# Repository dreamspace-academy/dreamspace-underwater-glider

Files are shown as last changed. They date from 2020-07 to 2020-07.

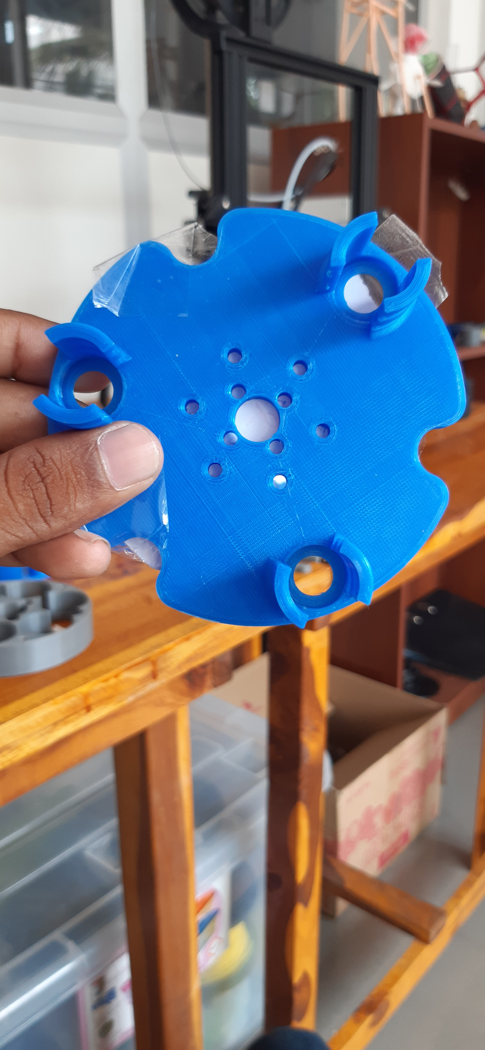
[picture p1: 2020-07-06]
images/printing-parts/underwater-glider-dreamspace-21.jpg

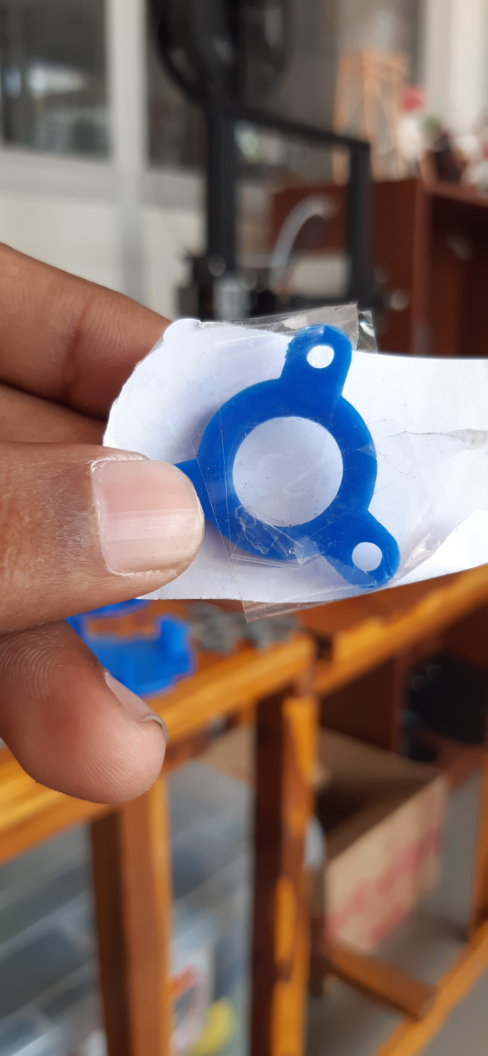
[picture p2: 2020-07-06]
images/printing-parts/underwater-glider-dreamspace-23.jpg

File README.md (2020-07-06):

# Underwater Glider



## **Motivation**

### Blue Econemy
Sri Lanka is an island country, located in the Indian Ocean, with a coastline of 1,585 km long, and the country claims an Exclusive Economic Zone (EEZ) extending 200 nautical miles, which is approximately 6.7 times Sri Lanka's land area. [1]

### Life Below Water
The world’s waters – their temperature, chemistry, currents and life – drive global systems that make the Earth habitable. How we manage this vital resource is essential for life on earth, and to counterbalance the effects of climate change. [2]

## **Problem**

### Real-time Monitoring
To keep our water ecosystem safe, secure, clean and sustainable, we need to measure various parameters in real-time. Sri Lanka, being a country that was devastated by 30 years of war, doesn’t even have the basic infrastructure, such as roads, in many parts of the country.

Therefore it is understandable that there is no modern infrastructure in Sri Lanka to measure and monitor the water ecosystems. Such equipment is very crucial for scientific research and assessment on an ecosystem, which is swiftly changing due to various weather conditions. [3]

### Affordability
The coastline and adjacent waters support highly productive marine ecosystems, and provide a massive economic value to this small nation, while this unique geographical position is highly contested by global powers.

## **Solution**

### Open-source Underwater Glider (OSUG)
There has been a breakthrough with low cost autonomous underwater vehicles, and as this capability has matured a wide range of hobby and commercial applications have been developed. However, there are no affordable extended duration underwater exploration platforms and this project aims to address this need.

Alex Williams, a young innovator from the USA, has developed a low cost and versatile underwater glider capable of extended missions of up to weeks at a time; using commodity hardware, 3D printed parts and an open-source autopilot. Furthermore, he won the Grand Prize in the Hackaday Prize Challenge 2017. [4]

### Underwater Gliding
Underwater gliders use a buoyancy engine to change the mass of the glider, allowing them to ascend and descend through the water. With power only being used to power the engine intermittently, gliders can typically run for weeks or months without recharge, making them ideal for environmental monitoring. As underwater gliders travel slowly through the water, they disturb the surrounding water very little, allowing for accurate and reliable data recording. [5]

underwater-glider-shanjeevan-dreamspace-7 (1)

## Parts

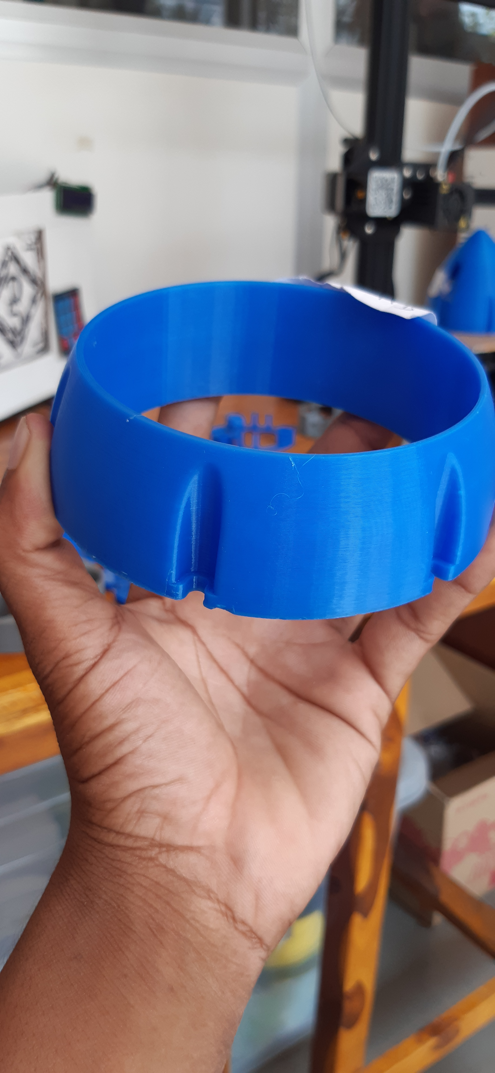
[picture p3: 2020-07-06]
images/printing-parts/underwater-glider-dreamspace-28.jpg

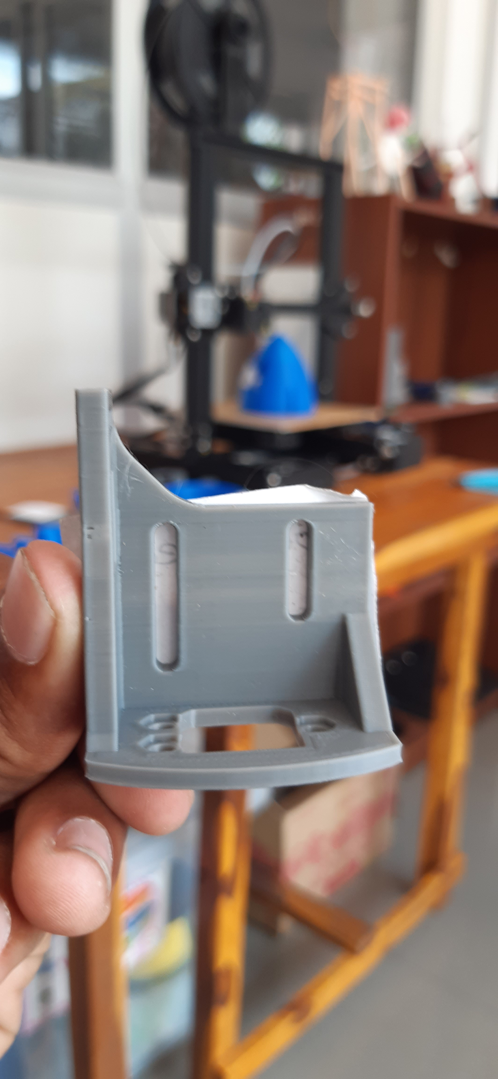
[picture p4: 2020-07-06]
images/printing-parts/underwater-glider-dreamspace-6.jpg

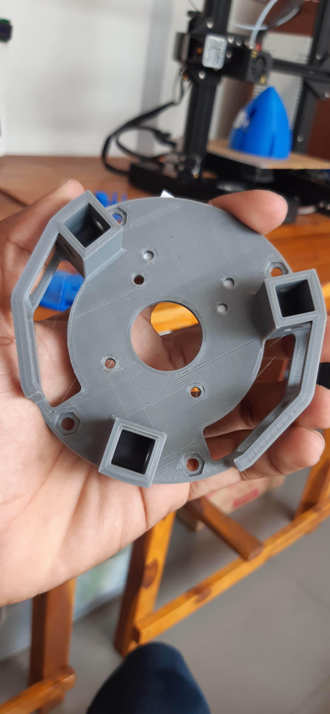
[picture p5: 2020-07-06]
images/printing-parts/underwater-glider-dreamspace-30.jpg

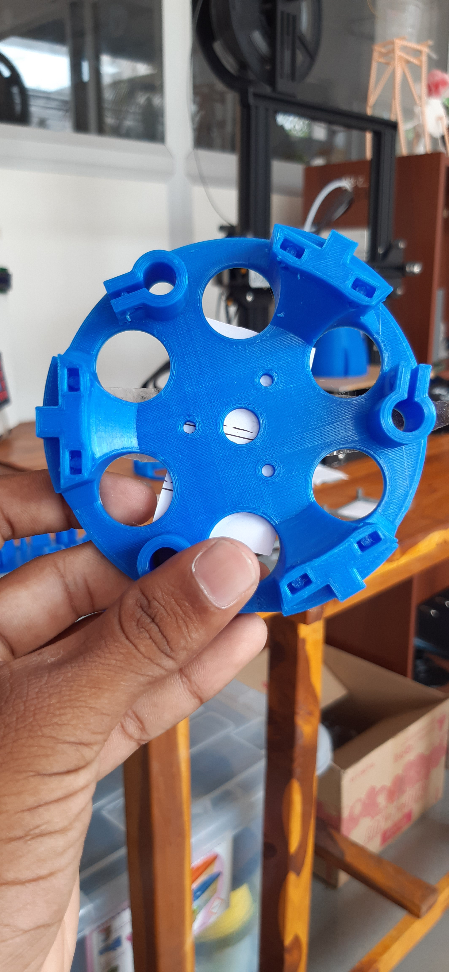
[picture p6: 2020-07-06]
images/printing-parts/underwater-glider-dreamspace-24.jpg

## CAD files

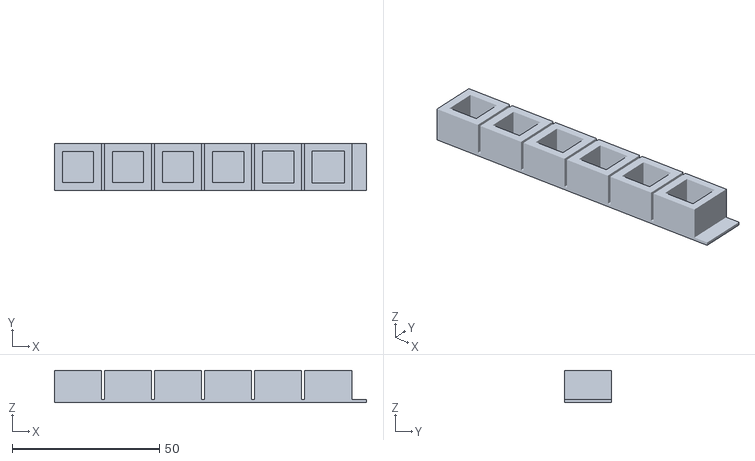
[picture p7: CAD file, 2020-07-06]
manufacture/3d-printing-parts/test-pieces/test-pieces-alum-tubing.stl
106.0 x 16.0 x 11.0

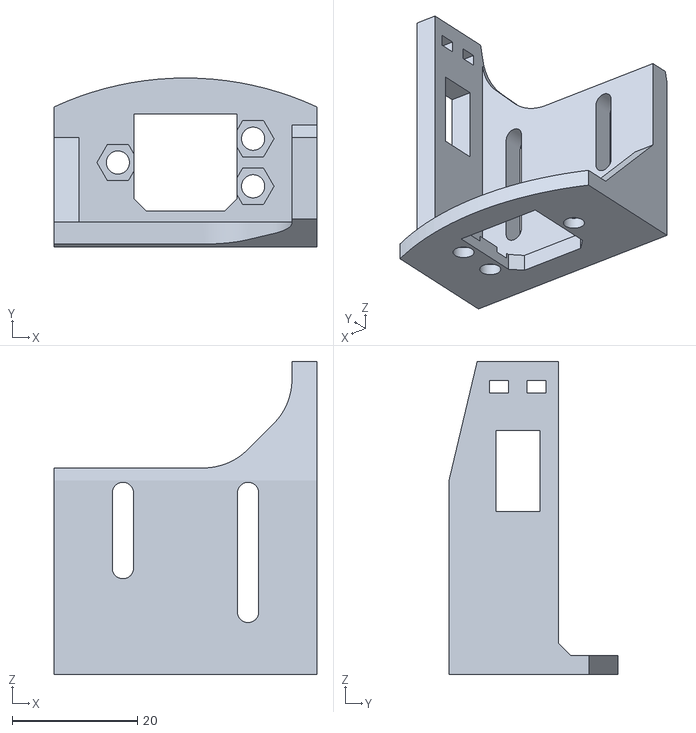
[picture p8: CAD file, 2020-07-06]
manufacture/3d-printing-parts/pogo-header-back-mount.stl
42.0 x 27.0 x 50.0

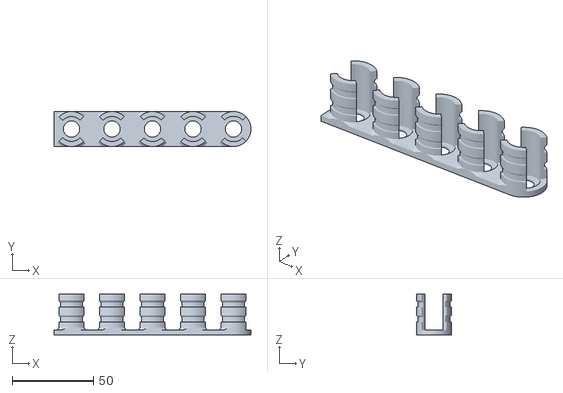
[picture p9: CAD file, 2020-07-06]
manufacture/3d-printing-parts/test-pieces/test-pieces-lm8uu.stl
121.6 x 21.6 x 25.0

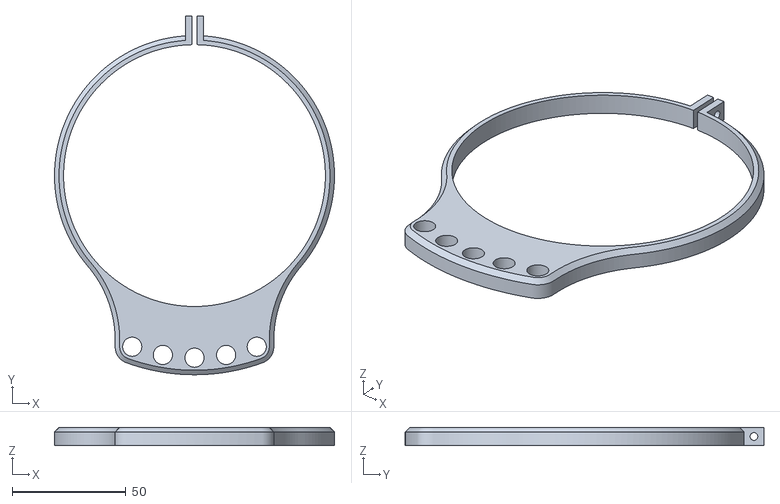
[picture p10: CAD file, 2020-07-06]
manufacture/3d-printing-parts/exterior-bar-mount.stl
123.0 x 157.5 x 8.00

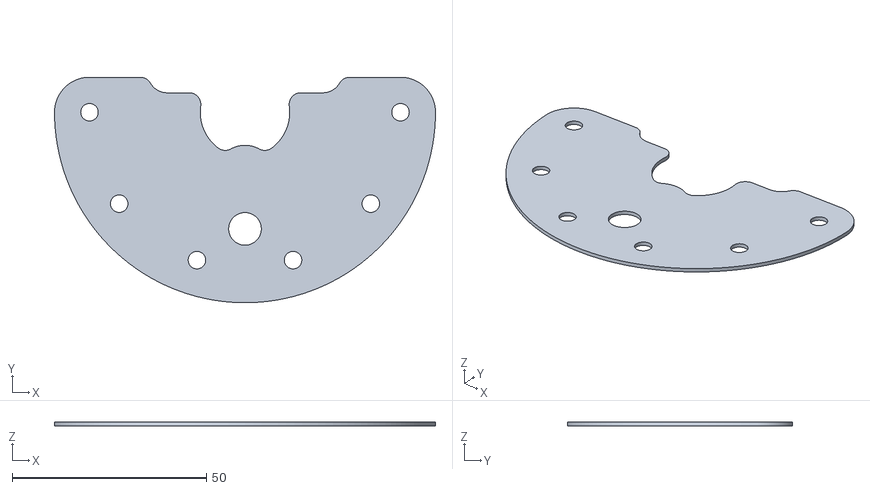
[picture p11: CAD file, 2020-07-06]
manufacture/3d-printing-parts/battery-rods-cover.stl
98.0 x 58.0 x 1.00

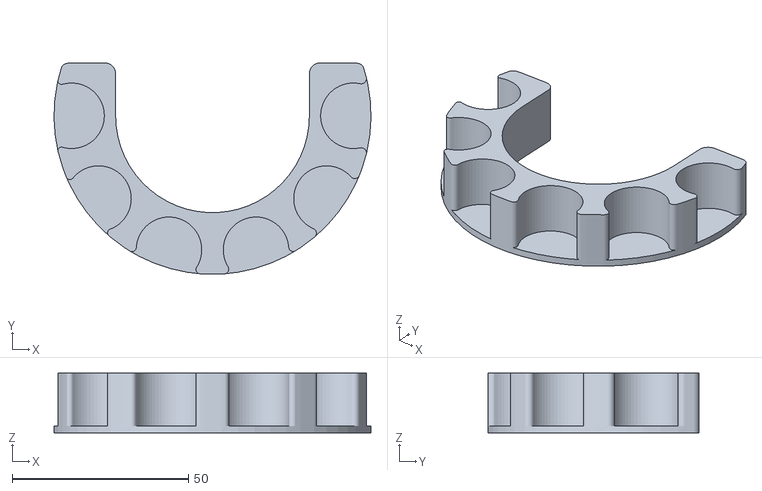
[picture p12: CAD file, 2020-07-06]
manufacture/3d-printing-parts/test-pieces/test-pieces-18650-fillet.stl
90.0 x 59.9 x 17.0

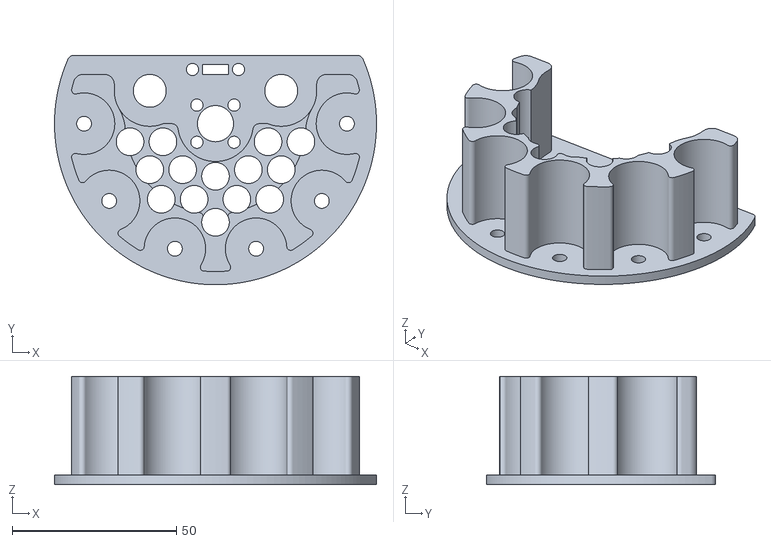
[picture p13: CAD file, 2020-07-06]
manufacture/3d-printing-parts/battery-mount-acme.stl
98.0 x 69.8 x 33.0

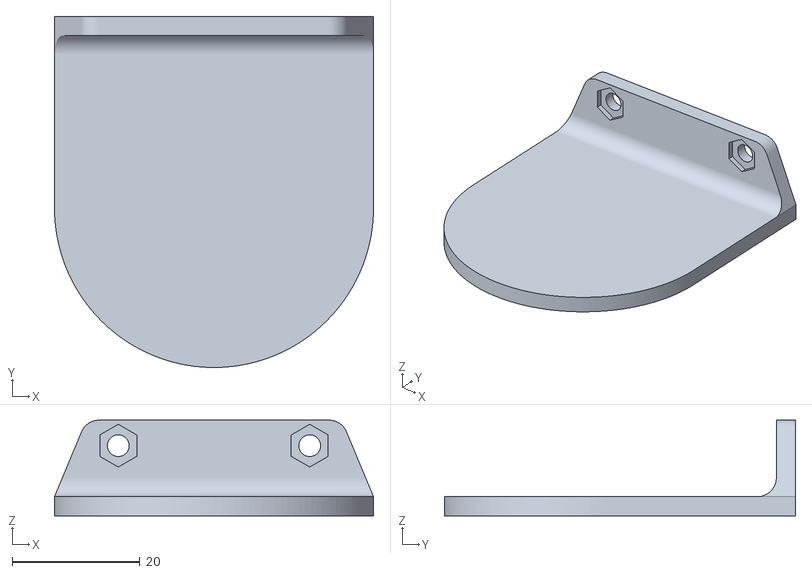
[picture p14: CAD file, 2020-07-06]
manufacture/3d-printing-parts/gps-mounting-plate.stl
50.0 x 55.0 x 15.0

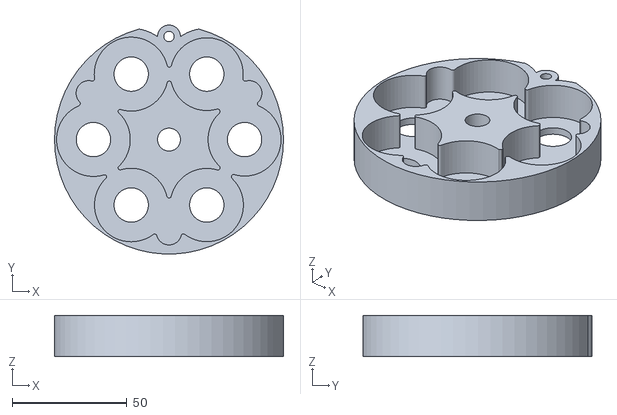
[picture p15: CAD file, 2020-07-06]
manufacture/3d-printing-parts/test-pieces/test-pieces-syringes.stl
100.0 x 99.9 x 18.0

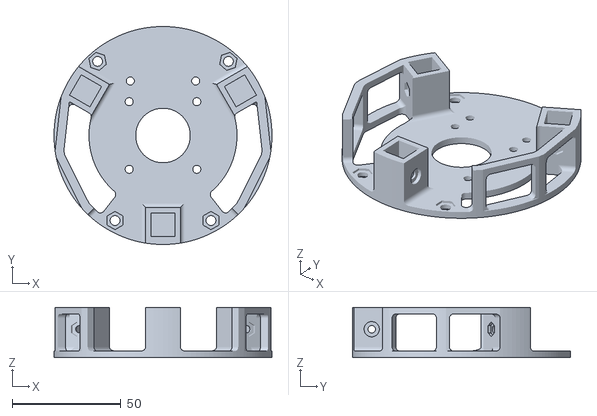
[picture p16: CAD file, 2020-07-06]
manufacture/3d-printing-parts/roll-motor-mount.stl
100.0 x 100.0 x 23.0

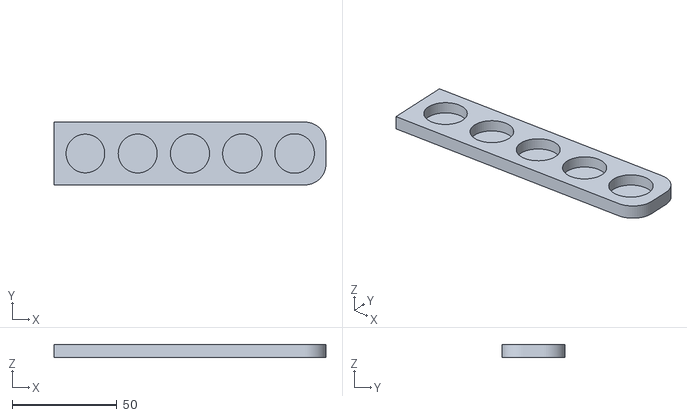
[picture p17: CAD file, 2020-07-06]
manufacture/3d-printing-parts/test-pieces/test-pieces-18650-diam.stl
130.0 x 30.0 x 6.00

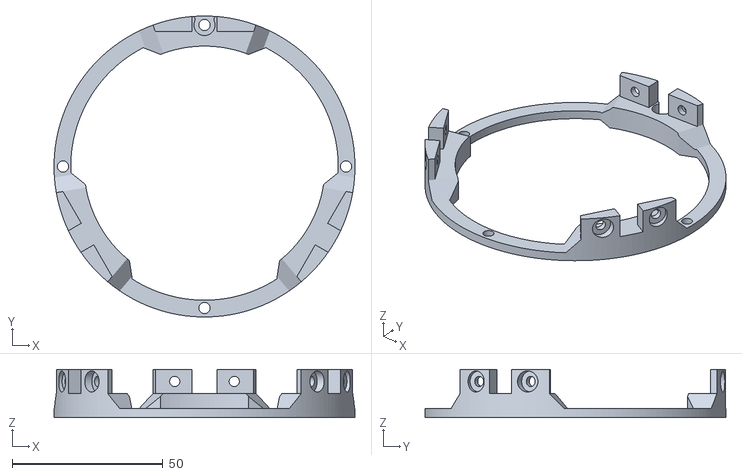
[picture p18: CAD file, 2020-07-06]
manufacture/3d-printing-parts/engine-endcap-mount.stl
100.0 x 100.0 x 16.0

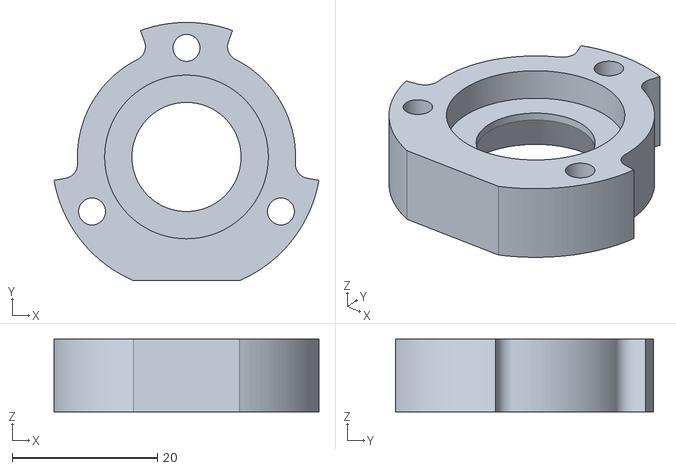
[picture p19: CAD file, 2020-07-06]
manufacture/3d-printing-parts/acme-bearing-back.stl
36.4 x 35.5 x 10.0

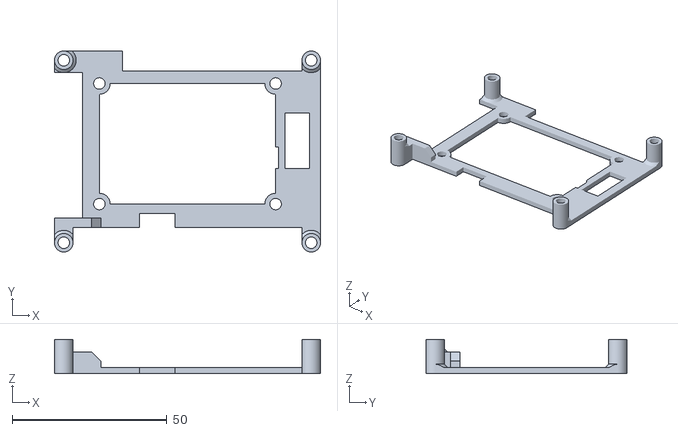
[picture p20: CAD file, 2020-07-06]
manufacture/3d-printing-parts/fathom-s-mounting-bracket.stl
86.0 x 65.0 x 11.0

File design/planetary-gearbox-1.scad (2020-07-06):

// Planetary gear bearing (customizable)

//

// clearance
tol=0.25;


M3_bolt_v_diam = 3.4;

M4_bolt_h_diam = 4.7;

M3_nut_v_diam = 6.7;


//End of edittable values

total_diameter_of_gearbox = 100;
// outer diameter of ring
D=75;
// thickness
T=10;

number_of_planets=3;
number_of_teeth_on_planets=7    ;
approximate_number_of_teeth_on_sun=11;
// pressure angle
P=45;//[30:60]
// number of teeth to twist across
nTwist=0.4;
// width of hexagonal hole
w=6.7;

DR=0.5*1;// maximum depth ratio of teeth

m=round(number_of_planets);
np=round(number_of_teeth_on_planets);
ns1=approximate_number_of_teeth_on_sun;
k1=round(2/m*(ns1+np));
k= k1*m%2!=0 ? k1+1 : k1;
ns=k*m/2-np;
echo(ns);
nr=ns+2*np;
pitchD=0.9*D/(1+min(PI/(2*nr*tan(P)),PI*DR/nr));
pitch=pitchD*PI/nr;
echo(pitch);
helix_angle=atan(2*nTwist*pitch/T);
echo(helix_angle);

phi=$t*360/m;


translate([0,0,10]){
    difference(){
        intersection(){
            difference(){
                cylinder(r=total_diameter_of_gearbox/2, h=20, center=true, $fn=100); 
                cylinder(r=D/2,h=50,center=true,$fn=100);
            }
            union(){
                translate([total_diameter_of_gearbox/2,0,0]){
                    cylinder(r=total_diameter_of_gearbox/2, h=50, center=true, $fn=6);
                }
                mirror([1,0,0]){
                    translate([total_diameter_of_gearbox/2,0,0]){
                        cylinder(r=total_diameter_of_gearbox/2, h=50, center=true, $fn=4);
                    }
                }
            }
        }
        
    translate([34,30,-15]){
        cylinder(r=M4_bolt_h_diam/2, h=30, $fn=100);
    }
    mirror([0,1,0]){
        translate([34,30,-15]){
            cylinder(r=M4_bolt_h_diam/2, h=30, $fn=100);
        }
    }
    translate([-39,22,-15]){
        cylinder(r=M4_bolt_h_diam/2, h=30, $fn=100);
    }
    mirror([0,1,0]){
        translate([-39,22,-15]){
            cylinder(r=M4_bolt_h_diam/2, h=30, $fn=100);
        }
    }
    }
}


  
translate([0,0,T/2]){
        union(){
            difference(){
                cylinder(r=D/2,h=T,center=true,$fn=100);
                herringbone(nr,pitch,P,DR,-tol,helix_angle,T+0.2,false);
                difference(){
                    translate([0,-D/2,0])rotate([90,0,0])monogram(h=10);
                    cylinder(r=D/2-0.25,h=T+2,center=true,$fn=100);
                }
            }
            rotate([0,0,(np+1)*180/ns+phi*(ns+np)*2/ns])
            difference(){
                mirror([0,1,0])
                    herringbone(ns,pitch,P,DR,tol,helix_angle,T,true);
                cylinder(r=2.5,h=50,center=true,$fn=100);
            }
            for(i=[1:m])rotate([0,0,i*360/m+phi])translate([pitchD/2*(ns+np)/nr,0,0])
                rotate([0,0,i*ns/m*360/np-phi*(ns+np)/np-phi])
                    herringbone(np,pitch,P,DR,tol,helix_angle,T,true);
        }
}

translate([0,0,14]){
    difference()
    {
        union(){
            difference()
            {
                cube(size=[19, 16, 10], center=true);
                cube(size=[22, 2, 10], center=true);
                cylinder(h=12, r=2.5, center=true, $fn=100);
                
                rotate([90, 0, 0]){
                    translate([5,1,0])cylinder(h=24, r=M3_bolt_v_diam/2, center=true, $fn=100);
                    translate([5,1,8])cylinder(h=2.5, r=3.5, center=true, $fn=100);
                    translate([5,1,-8])cylinder(h=M3_nut_v_diam/2, r=3.35, center=true, $fn=6);
                    mirror([1,0,0]){
                        translate([5,1,0])cylinder(h=24, r=M3_bolt_v_diam/2, center=true, $fn=100);
                        translate([5,1,8])cylinder(h=2.5, r=3.5, center=true, $fn=100);
                        translate([5,1,-8])cylinder(h=M3_nut_v_diam/2, r=3.35, center=true, $fn=6);
                    }
                }
            }
            
        }
//        rotate([0, 90, 0]){
//            translate([6,8,0])cylinder(h=20, r=3, center=true, $fn=4);
//            mirror([0,1,0]){
//                translate([6,8,0])cylinder(h=20, r=3, center=true, $fn=4);
//            }
//        }
    }
} 

module rack(
	number_of_teeth=15,
	circular_pitch=10,
	pressure_angle=28,
	helix_angle=0,
	clearance=0,
	gear_thickness=5,
	flat=false){
addendum=circular_pitch/(4*tan(pressure_angle));

flat_extrude(h=gear_thickness,flat=flat)translate([0,-clearance*cos(pressure_angle)/2])
	union(){
		translate([0,-0.5-addendum])square([number_of_teeth*circular_pitch,1],center=true);
		for(i=[1:number_of_teeth])
			translate([circular_pitch*(i-number_of_teeth/2-0.5),0])
			polygon(points=[[-circular_pitch/2,-addendum],[circular_pitch/2,-addendum],[0,addendum]]);
	}
}

module monogram(h=1)
linear_extrude(height=h,center=true)
translate(-[3,2.5])union(){
	difference(){
		translate([1,10])square([2,3]);
	}
}

module herringbone(
	number_of_teeth=15,
	circular_pitch=10,
	pressure_angle=28,
	depth_ratio=1,
	clearance=0,
	helix_angle=0,
	gear_thickness=5,
    hollow_centre = true){
union(){
	gear(number_of_teeth,
		circular_pitch,
		pressure_angle,
		depth_ratio,
		clearance,
		helix_angle,
		gear_thickness/2,
        false,
        hollow_centre);
	mirror([0,0,1])
		gear(number_of_teeth,
			circular_pitch,
			pressure_angle,
			depth_ratio,
			clearance,
			helix_angle,
			gear_thickness/2,
            false,
            hollow_centre);
}}

module gear (
	number_of_teeth=15,
	circular_pitch=10,
	pressure_angle=28,
	depth_ratio=1,
	clearance=0,
	helix_angle=0,
	gear_thickness=5,
	flat=false,
    hollow_centre=true){
difference(){
    pitch_radius = number_of_teeth*circular_pitch/(2*PI);
    twist=tan(helix_angle)*gear_thickness/pitch_radius*180/PI;

    flat_extrude(h=gear_thickness,twist=twist,flat=flat)
        gear2D (
            number_of_teeth,
            circular_pitch,
            pressure_angle,
            depth_ratio,
            clearance);
    if(hollow_centre == true){
        cylinder (h = 20, r=M4_bolt_h_diam/2, center = true, $fn=100);
    }
}
}

module flat_extrude(h,twist,flat){
	if(flat==false)
		linear_extrude(height=h,twist=twist,slices=twist/6)children(0);
	else
		children(0);
}

module gear2D (
	number_of_teeth,
	circular_pitch,
	pressure_angle,
	depth_ratio,
	clearance){
pitch_radius = number_of_teeth*circular_pitch/(2*PI);
base_radius = pitch_radius*cos(pressure_angle);
depth=circular_pitch/(2*tan(pressure_angle));
outer_radius = clearance<0 ? pitch_radius+depth/2-clearance : pitch_radius+depth/2;
root_radius1 = pitch_radius-depth/2-clearance/2;
root_radius = (clearance<0 && root_radius1<base_radius) ? base_radius : root_radius1;
backlash_angle = clearance/(pitch_radius*cos(pressure_angle)) * 180 / PI;
half_thick_angle = 90/number_of_teeth - backlash_angle/2;
pitch_point = involute (base_radius, involute_intersect_angle (base_radius, pitch_radius));
pitch_angle = atan2 (pitch_point[1], pitch_point[0]);
min_radius = max (base_radius,root_radius);

intersection(){
	rotate(90/number_of_teeth)
		circle($fn=number_of_teeth*3,r=pitch_radius+depth_ratio*circular_pitch/2-clearance/2);
	union(){
		rotate(90/number_of_teeth)
			circle($fn=number_of_teeth*2,r=max(root_radius,pitch_radius-depth_ratio*circular_pitch/2-clearance/2));
		for (i = [1:number_of_teeth])rotate(i*360/number_of_teeth){
			halftooth (
				pitch_angle,
				base_radius,
				min_radius,
				outer_radius,
				half_thick_angle);		
			mirror([0,1])halftooth (
				pitch_angle,
				base_radius,
				min_radius,
				outer_radius,
				half_thick_angle);
		}
	}
}}

module halftooth (
	pitch_angle,
	base_radius,
	min_radius,
	outer_radius,
	half_thick_angle){
index=[0,1,2,3,4,5];
start_angle = max(involute_intersect_angle (base_radius, min_radius)-5,0);
stop_angle = involute_intersect_angle (base_radius, outer_radius);
angle=index*(stop_angle-start_angle)/index[len(index)-1];
p=[[0,0],
	involute(base_radius,angle[0]+start_angle),
	involute(base_radius,angle[1]+start_angle),
	involute(base_radius,angle[2]+start_angle),
	involute(base_radius,angle[3]+start_angle),
	involute(base_radius,angle[4]+start_angle),
	involute(base_radius,angle[5]+start_angle)];

difference(){
	rotate(-pitch_angle-half_thick_angle)polygon(points=p);
	square(2*outer_radius);
}}

// Mathematical Functions
//===============

// Finds the angle of the involute about the base radius at the given distance (radius) from it's center.
//source: http://www.mathhelpforum.com/math-help/geometry/136011-circle-involute-solving-y-any-given-x.html

function involute_intersect_angle (base_radius, radius) = sqrt (pow (radius/base_radius, 2) - 1) * 180 / PI;

// Calculate the involute position for a given base radius and involute angle.

function involute (base_radius, involute_angle) =
[
	base_radius*(cos (involute_angle) + involute_angle*PI/180*sin (involute_angle)),
	base_radius*(sin (involute_angle) - involute_angle*PI/180*cos (involute_angle))
];

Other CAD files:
manufacture/3d-printing-parts/battery-mount-bearings.stl
manufacture/3d-printing-parts/pogo-header-slider-mount.stl
manufacture/3d-printing-parts/syringe-clamp-front.stl
manufacture/3d-printing-parts/engine-end-connector.stl
manufacture/3d-printing-parts/acme-bearing-front.stl
manufacture/3d-printing-parts/acme-motor-connector.stl
manufacture/3d-printing-parts/battery-mount-connector.stl
manufacture/3d-printing-parts/buoyancy-engine-bearing-plate.stl
manufacture/3d-printing-parts/buoyancy-engine-motor-mount.stl
manufacture/3d-printing-parts/cable-chain-nut-holder.stl
manufacture/3d-printing-parts/circuit-rack-end.stl
manufacture/3d-printing-parts/circuit-rack-endcap-mount.stl
manufacture/3d-printing-parts/engine-bearing-fastener.stl
manufacture/3d-printing-parts/engine-endstop.stl
manufacture/3d-printing-parts/pitch-motor-back-plate.stl
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

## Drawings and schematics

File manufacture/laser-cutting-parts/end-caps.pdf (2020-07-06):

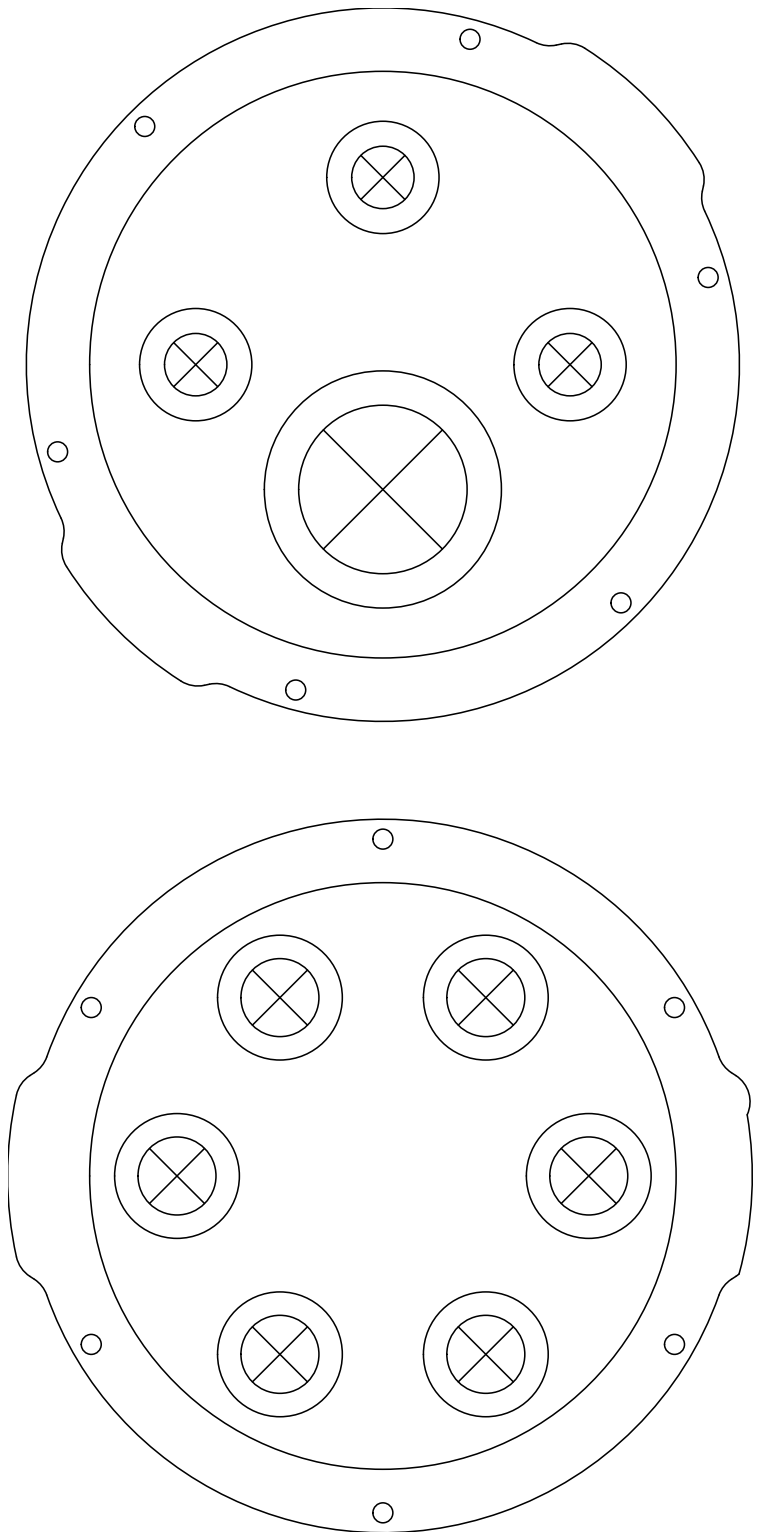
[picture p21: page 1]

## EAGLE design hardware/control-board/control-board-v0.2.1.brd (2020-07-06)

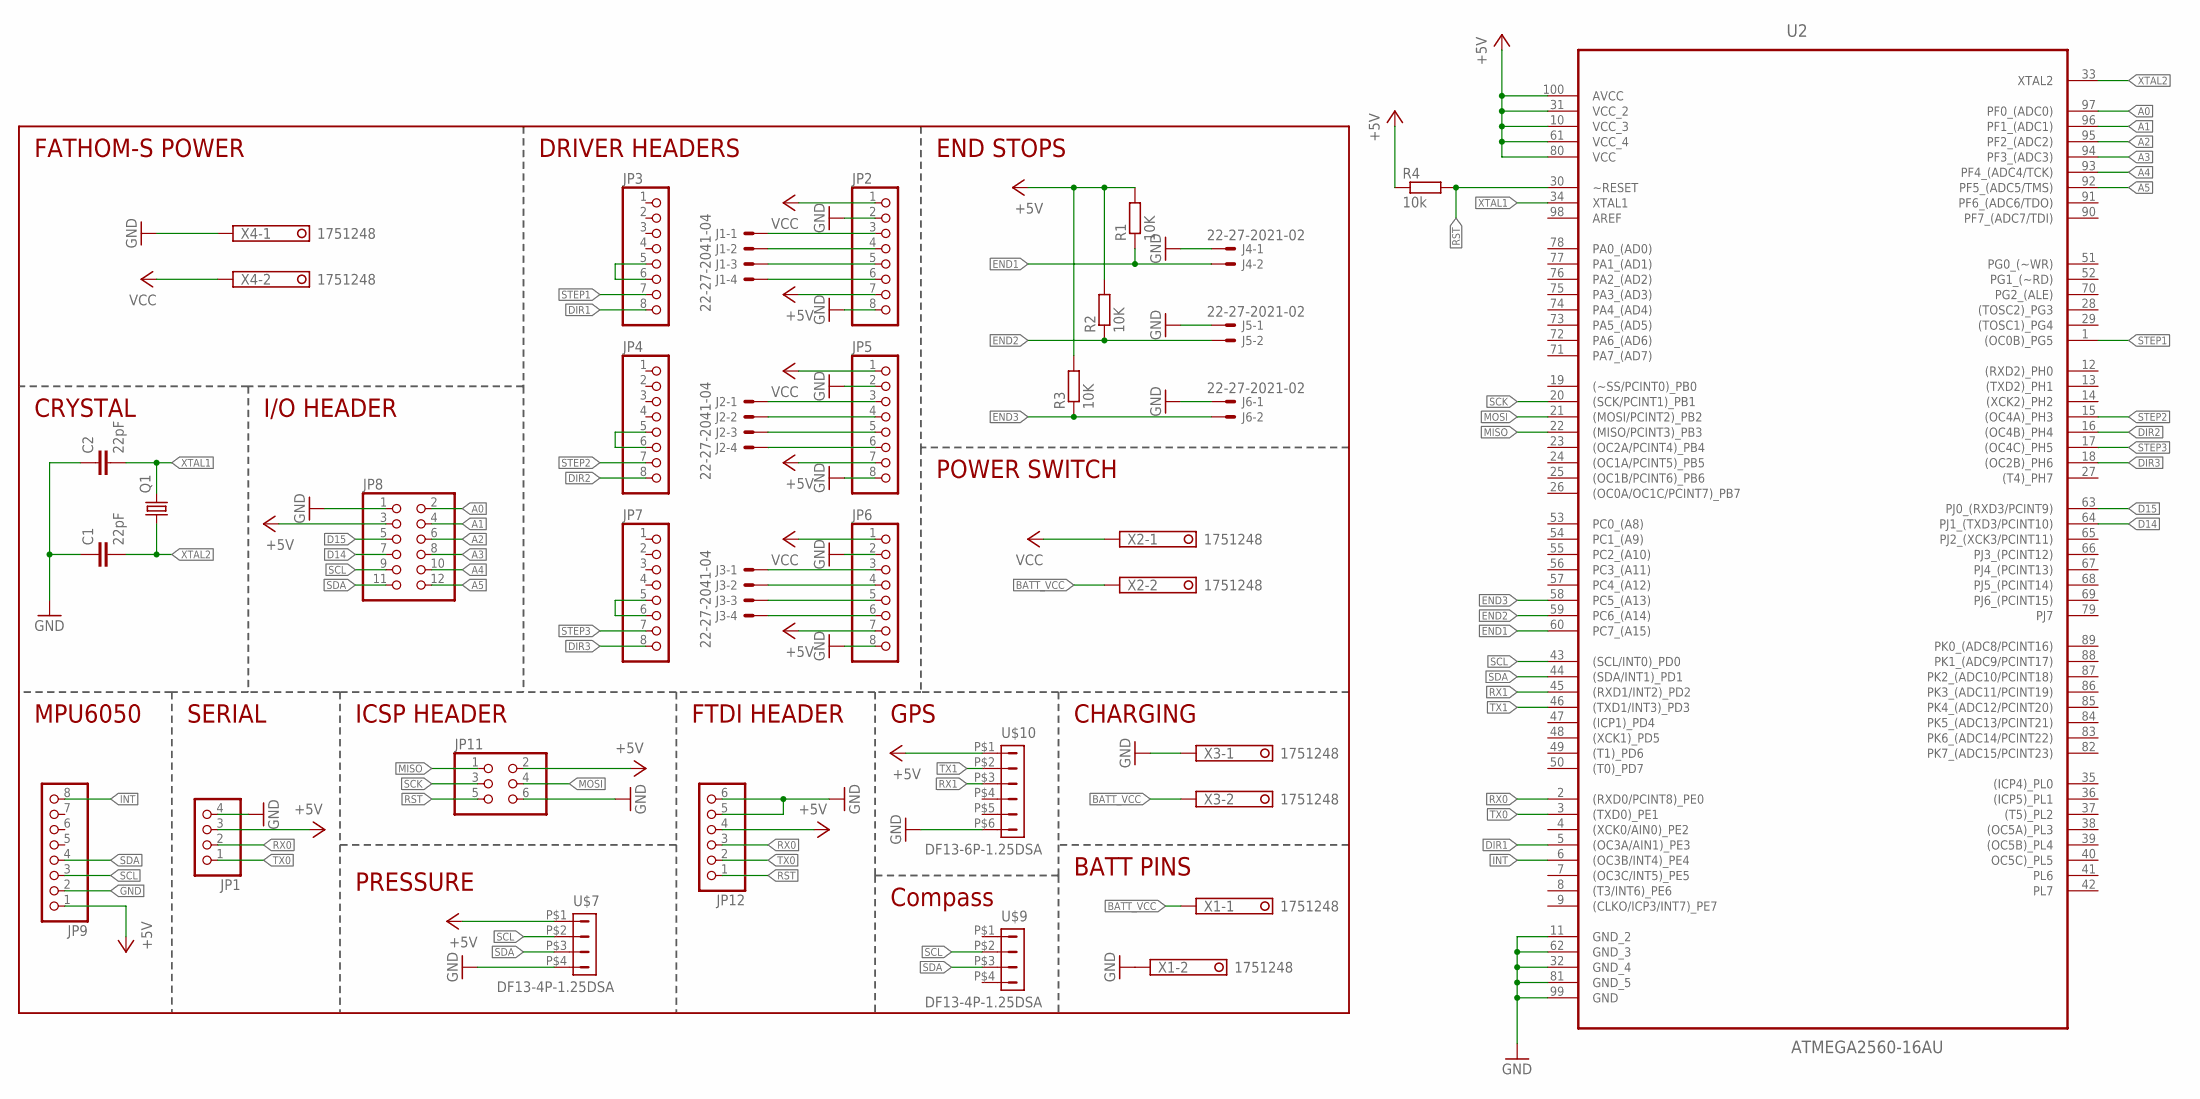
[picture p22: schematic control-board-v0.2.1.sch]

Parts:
C1, C2: 22pF; C0603
J1, J2, J3: 22-27-2041-04; 6410-04
J4, J5, J6: 22-27-2021-02; 6410-02
JP1: PINHD-1X4; 1X04
JP2, JP3, JP4, JP5, JP6, JP7, JP9: PINHD-1X8; 1X08
JP8: PINHD-2X6; 2X06
JP11: PINHD-2X3; 2X03
JP12: PINHD-1X6; 1X06
Q1: CRYSTALHC49U70; HC49U70
R1, R2, R3: 10K; R0603
R4: 10k; R0603
U2: ATMEGA2560-16AU; QFP50P1600X1600X120-100N
U$7, U$9: DF13-4P-1.25DSA
U$10: DF13-6P-1.25DSA
X1, X2, X3, X4: 1751248

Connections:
+5V: JP1.3, JP2.7, JP5.7, JP6.7, JP8.3, JP9.1, JP11.2, JP12.4, R1.2, R2.2, R3.2, R4.1, U2.10 (VCC_3), U2.31 (VCC_2), U2.61 (VCC_4), U2.80 (VCC), U2.100 (AVCC), U$7.P$1 (1), U$10.P$1 (1)
A0: JP8.2, U2.97 (PF0_(ADC0))
A1: JP8.4, U2.96 (PF1_(ADC1))
A2: JP8.6, U2.95 (PF2_(ADC2))
A3: JP8.8, U2.94 (PF3_(ADC3))
A4: JP8.10, U2.93 (PF4_(ADC4/TCK))
A5: JP8.12, U2.92 (PF5_(ADC5/TMS))
BATT_VCC: X1.1, X2.2, X3.2
D14: JP8.7, U2.64 (PJ1_(TXD3/PCINT10))
D15: JP8.5, U2.63 (PJ0_(RXD3/PCINT9))
DIR1: JP3.8, U2.5 ((OC3A/AIN1)_PE3)
DIR2: JP4.8, U2.16 ((OC4B)_PH4)
DIR3: JP7.8, U2.18 ((OC2B)_PH6)
END1: J4.2, R1.1, U2.60 (PC7_(A15))
END2: J5.2, R2.1, U2.59 (PC6_(A14))
END3: J6.2, R3.1, U2.58 (PC5_(A13))
GND: C1.1, C2.1, J4.1, J5.1, J6.1, JP1.4, JP2.2, JP2.8, JP5.2, JP5.8, JP6.2, JP6.8, JP8.1, JP9.2, JP11.6, JP12.5, JP12.6, U2.11 (GND_2), U2.32 (GND_4), U2.62 (GND_3), U2.81 (GND_5), U2.99 (GND), U$7.P$4 (4), U$10.P$6 (6), X1.2, X3.1, X4.1
INT: JP9.8, U2.6 ((OC3B/INT4)_PE4)
MISO: JP11.1, U2.22 ((MISO/PCINT3)_PB3)
MOSI: JP11.4, U2.21 ((MOSI/PCINT2)_PB2)
unnamed: JP3.5, JP3.6
unnamed: JP4.5, JP4.6
unnamed: J1.4, JP2.6
unnamed: JP7.5, JP7.6
unnamed: J1.3, JP2.5
unnamed: J1.2, JP2.4
unnamed: J1.1, JP2.3
unnamed: J2.4, JP5.6
unnamed: J2.3, JP5.5
unnamed: J2.2, JP5.4
unnamed: J2.1, JP5.3
unnamed: J3.4, JP6.6
unnamed: J3.3, JP6.5
unnamed: J3.2, JP6.4
unnamed: J3.1, JP6.3
RST: JP11.5, JP12.1, R4.2, U2.30 (~RESET)
RX0: JP1.2, JP12.3, U2.2 ((RXD0/PCINT8)_PE0)
RX1: U2.45 ((RXD1/INT2)_PD2), U$10.P$3 (3)
SCK: JP11.3, U2.20 ((SCK/PCINT1)_PB1)
SCL: JP8.9, JP9.3, U2.43 ((SCL/INT0)_PD0), U$7.P$2 (2), U$9.P$2 (2)
SDA: JP8.11, JP9.4, U2.44 ((SDA/INT1)_PD1), U$7.P$3 (3), U$9.P$3 (3)
STEP1: JP3.7, U2.1 ((OC0B)_PG5)
STEP2: JP4.7, U2.15 ((OC4A)_PH3)
STEP3: JP7.7, U2.17 ((OC4C)_PH5)
TX0: JP1.1, JP12.2, U2.3 ((TXD0)_PE1)
TX1: U2.46 ((TXD1/INT3)_PD3), U$10.P$2 (2)
VCC: JP2.1, JP5.1, JP6.1, X2.1, X4.2
XTAL1: C2.2, Q1.2, U2.34 (XTAL1)
XTAL2: C1.2, Q1.1, U2.33 (XTAL2)

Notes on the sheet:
MPU6050
DRIVER HEADERS
BATT PINS
END STOPS
SERIAL
ICSP HEADER
FTDI HEADER
GPS
Compass
CHARGING
PRESSURE
POWER SWITCH
FATHOM-S POWER
CRYSTAL
I/O HEADER

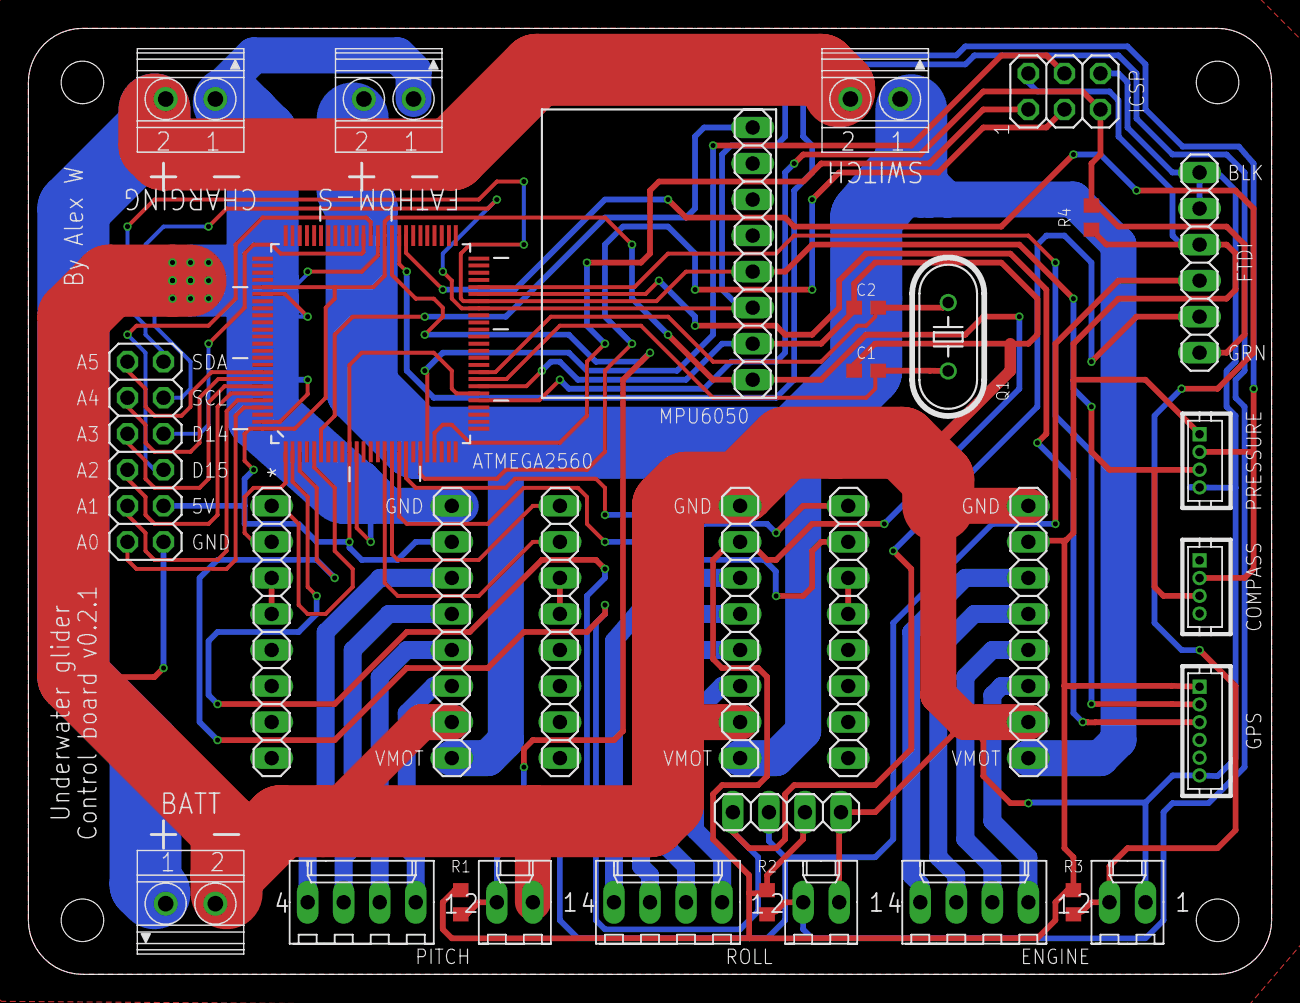
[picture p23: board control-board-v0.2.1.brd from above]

Board: 2 copper layers, 87.6 x 66.7 mm, 32 parts (0 on the bottom side), 49 nets.

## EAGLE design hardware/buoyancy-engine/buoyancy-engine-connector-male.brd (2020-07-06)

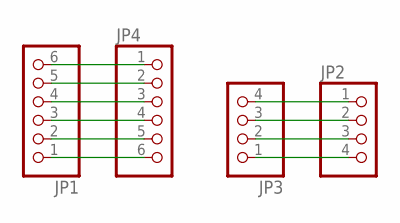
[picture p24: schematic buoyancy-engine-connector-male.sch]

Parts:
JP1, JP4: PINHD-1X6; 1X06
JP2, JP3: PINHD-1X4; 1X04

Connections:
unnamed: JP2.1, JP3.4
unnamed: JP2.2, JP3.3
unnamed: JP2.3, JP3.2
unnamed: JP2.4, JP3.1
unnamed: JP1.6, JP4.1
unnamed: JP1.5, JP4.2
unnamed: JP1.4, JP4.3
unnamed: JP1.3, JP4.4
unnamed: JP1.2, JP4.5
unnamed: JP1.1, JP4.6

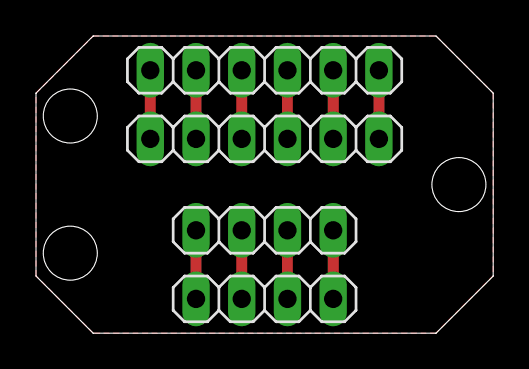
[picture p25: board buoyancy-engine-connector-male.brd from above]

Board: 2 copper layers, 25.4 x 16.5 mm, 4 parts (0 on the bottom side), 10 nets.

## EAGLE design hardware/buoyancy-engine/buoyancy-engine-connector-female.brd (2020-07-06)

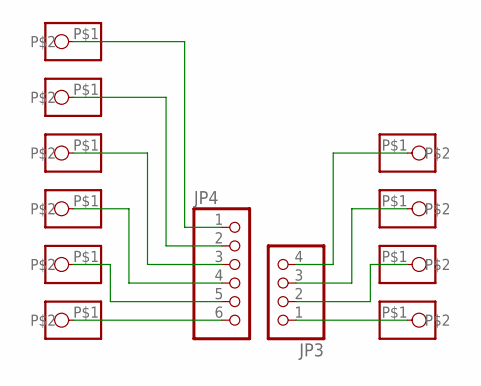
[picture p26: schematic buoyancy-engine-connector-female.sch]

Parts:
JP3: PINHD-1X4; 1X04
JP4: PINHD-1X6; 1X06
U$1, U$2, U$3, U$4, U$5, U$6, U$7, U$8, U$9, U$10: POGO-PIN-PAD

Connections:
unnamed: JP3.4, U$10.P$1
unnamed: JP3.3, U$7.P$1
unnamed: JP3.2, U$8.P$1
unnamed: JP3.1, U$9.P$1
unnamed: JP4.1, U$6.P$1
unnamed: JP4.2, U$5.P$1
unnamed: JP4.3, U$4.P$1
unnamed: JP4.4, U$3.P$1
unnamed: JP4.5, U$2.P$1
unnamed: JP4.6, U$1.P$1

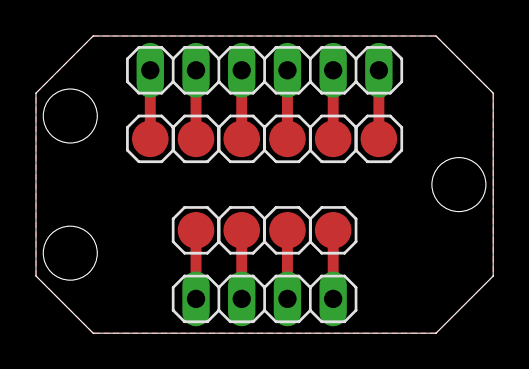
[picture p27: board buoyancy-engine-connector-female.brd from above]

Board: 2 copper layers, 25.4 x 16.5 mm, 12 parts (0 on the bottom side), 10 nets.

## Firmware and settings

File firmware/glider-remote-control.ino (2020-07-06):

const int stepPitchPin = 4;
const int dirPitchPin = 5;
const int endStopPitchPin = 30;

const int stepRollPin = 6;
const int dirRollPin = 7;
const int endStopRollPin = 31;

const int stepEnginePin = 8;
const int dirEnginePin = 9;
const int endStopEnginePin = 32;

const int forwardDir = 0;
const int reverseDir = 1;

int pitchPos;
int pitchMax = 2800;
int pitchDelay = 900;
int rollPos;
int rollMax = 50;
int rollDelay = 3000;
int enginePos;
int engineMax = 1900;
int engineDelay = 1100;

void setup() {
  pinMode(stepRollPin, OUTPUT);
  pinMode(dirRollPin, OUTPUT);

  pinMode(stepPitchPin, OUTPUT);
  pinMode(dirPitchPin, OUTPUT);

  pinMode(stepEnginePin, OUTPUT);
  pinMode(dirEnginePin, OUTPUT);

  homeAll();

  Serial.begin(115200);

}

boolean reachedEndStop(int endStop) {
  return (digitalRead(endStop) == 0);
}

boolean dirForward(int dir) {
  return (dir == 0);
}

int runMotor(int stepPin, int dirPin, int endStop, int dir, int amountToMove, int currentPos, int maxPos, int motorDelay) {
  digitalWrite(dirPin, dir);
  for (int x = 0; x < amountToMove; x++) {
    if (dirForward(dir) && reachedEndStop(endStop) ) {
      return 0;
    }
    if (!dirForward(dir) && (currentPos + 1 > maxPos)) {
      break;
    }

    digitalWrite(stepPin, HIGH);
    delayMicroseconds(motorDelay);
    digitalWrite(stepPin, LOW);
    delayMicroseconds(motorDelay);

    if (dirForward(dir)) {
      currentPos += -1;
    } else {
      currentPos += 1;
    }
  }
  return currentPos;
}

void diagnosticOutput () {
  Serial.print("Roll end stop: ");
  Serial.print(digitalRead(endStopRollPin));
  Serial.print(", pitch end stop: ");
  Serial.print(digitalRead(endStopPitchPin));
  Serial.print(", engine end stop: ");
  Serial.print(digitalRead(endStopEnginePin));
  Serial.println();
  Serial.print("Roll pos: ");
  Serial.print(rollPos);
  Serial.print(", Pitch pos: ");
  Serial.print(pitchPos);
  Serial.print(", Engine pos: ");
  Serial.print(enginePos);
  Serial.println();

}

void homeAll () {
  // home, move the motors the maximum distance towards the endstop, if the actuator is closer than the far end the endstop will stop movement
  rollPos = runMotor(stepRollPin, dirRollPin, endStopRollPin, forwardDir, rollMax, rollPos, rollMax, rollDelay);
  pitchPos = runMotor(stepPitchPin, dirPitchPin, endStopPitchPin, forwardDir, pitchMax, pitchPos, pitchMax, pitchDelay);
  enginePos = runMotor(stepEnginePin, dirEnginePin, endStopEnginePin, forwardDir, engineMax, enginePos, engineMax, engineDelay);

}

void loop() {

  if (Serial.available() > 0) {

    int inByte = Serial.read();
    Serial.println(inByte);
    switch (inByte) {
      case 1:
        Serial.println("Disabled Rotating mass clockwise");
        rollPos = runMotor(stepRollPin, dirRollPin, endStopRollPin, reverseDir, 5, rollPos, rollMax, rollDelay);
        break;
      case 2:
        Serial.println("Disabled Rotating mass anticlockwise");
        rollPos = runMotor(stepRollPin, dirRollPin, endStopRollPin, forwardDir, 5, rollPos, rollMax, rollDelay);
        break;
      case 3:
        Serial.println("Mass forward");
        pitchPos = runMotor(stepPitchPin, dirPitchPin, endStopPitchPin, forwardDir, 900, pitchPos, pitchMax, pitchDelay);
        break;
      case 4:
        Serial.println("Mass backward");
        pitchPos = runMotor(stepPitchPin, dirPitchPin, endStopPitchPin, reverseDir, 900, pitchPos, pitchMax, pitchDelay);
        break;
      case 5:
        Serial.println("Plunger backward");
        enginePos = runMotor(stepEnginePin, dirEnginePin, endStopEnginePin, reverseDir, 100, enginePos, engineMax, engineDelay);
        break;
      case 6:
        Serial.println("Plunger forward");
        enginePos = runMotor(stepEnginePin, dirEnginePin, endStopEnginePin, forwardDir, 100, enginePos, engineMax, engineDelay);
        break;
      case 7:
        Serial.println("Homing");
        homeAll();
      default:
        Serial.println("None");

    }
    diagnosticOutput();
  }
}

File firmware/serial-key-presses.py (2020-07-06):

import serial;
from tkinter import *;
serial_commands = {"a" : 1, "d" : 2, "w" : 3, "s" : 4, "i" : 5, "k" : 6};
ser = serial.Serial();

def keyUp(e):
    global ser;
    if e.char in serial_commands.keys():
        print(e.char);
        ser.write(bytes([serial_commands[e.char]]));

def initialise():
    global ser;
    try:
        ser = serial.Serial('/dev/ttyUSB0');
        ser.baudrate = 115200;
    except Exception as e:
        raise Exception(e);

    root = Tk();
    root.bind("<KeyRelease>", keyUp);
    
    root.mainloop();

if __name__ == "__main__":
    initialise();

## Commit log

2020-07-06 Add 3d printing manufacturing files
    [acme_bearing_back.stl, acme_bearing_front.stl, acme_motor_connector.stl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]
2020-07-06 Add laser cutting parts
2020-07-06 Add gearbox design files
    [planetary-gearbox-1.scad, planetary-gearbox-2.scad]
2020-07-06 Add buoyancy engine eagle pcb design files
    [buoyancy-engine-connector-female.brd, buoyancy-engine-connector-female.sch, buoyancy-engine-connector-male.brd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]
2020-07-06 Add control board eagle pcb design files
    [control-board-v0.2.1.brd, control-board-v0.2.1.sch]
2020-07-06 Add pcb manufacturing files
2020-07-06 Clean files
    [acme-bearing-back.stl, acme-bearing-front.stl, acme-motor-connector.stl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]
2020-07-06 Add test 3d print files
    [test-pieces-18650-diam.stl, test-pieces-18650-fillet.stl, test-pieces-alum-tubing.stl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]
2020-07-06 Add docs files
    [components-quotation.xlsx]
2020-07-06 Move gdocs to the drive
    [components-quotation.xlsx]
